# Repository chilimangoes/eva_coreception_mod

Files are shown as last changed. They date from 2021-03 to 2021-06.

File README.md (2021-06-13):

# EVA Coreception Mod

EVA carriage mod for the Creativity ELF/ELF PRO and SainSmart Coreception lines of CoreXY 3D printers

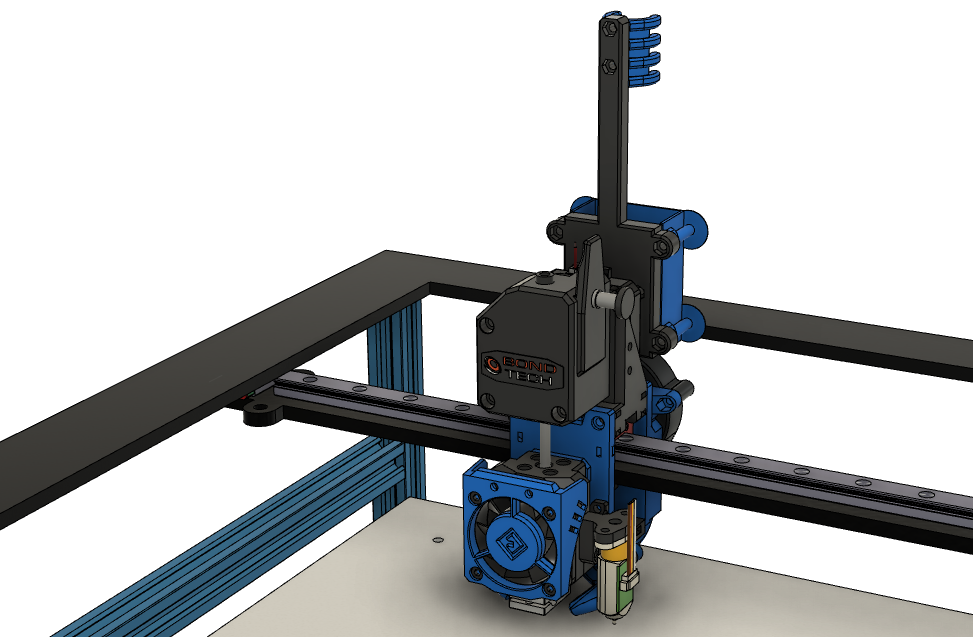
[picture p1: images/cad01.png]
CAD front view


## Overview

This is a mod for the EVA carriage platform to work on the Creativity ELF/ELF PRO and SainSmart Coreception lines of CoreXY 3D printers. However, the changes have been made in such a way as to try to increase the configurability of the tool head, making it adaptable to a wider range of printers. In particular, it should be trivial to adapt to other CoreXY printers with a "halo" design, similar to the ELF variants, such as the Two Trees Sapphire.

Overall print area on my Coreception, with this mod installed, is X=297mm, Y=294mm. I believe that moving the BL Touch to the middle, under the gantry, would increase the X travel by about 10mm. And filing down the M3 bolt hole on the rear blower fan, to allow the bolt head to sit flush with the fan casing, would give another ~3mm of Y travel on the rear.

Check out the [main EVA documentation site](https://main.eva-3d.page/) for more details on the EVA platform, information on printing and postprocessing parts, etc. Feel free to reach out to me on the ELF/Coreception Facebook group with questions or concerns.

## Files

STL files are under the [`/stl`](/stl) folder. You will need to select the appropriate [Face] mount for your hot end - V6, Dragon, or Mosquito. There is also an unofficial mount for the stock MK8 hot end [here](https://contrib.eva-3d.page/hotends/microswiss-mk8/). Start with one of the `"_mirrored"` hot end mounts if you plan on using the BL Touch on the the ELF/Coreception. If you're using the onofficial MK8 mount linked above, you'll need to mirror it yourself. I highly recommend printing out and test fitting everything *thoroughly* before disassembling your existing hot end and carriage. I also recommend printing out a spare set of parts, especially anything that is near or touching the hot end. It might also be a good idea to buy some new, higher quality belts before installing. My stock belts were pretty low quality and chewed up pretty badly by the zip ties used to secure them to the stock carriage.

There are multiple versions of the Y end stop (`end_stop_y_XXmm_offset.stl`) with a range of offsets, to allow people to find tune their Y=0 (I figure there may be manufacturing variances). On my machine, I ended up with either a 6mm or 7mm offset. They're a quick print, so I would recommend starting with the 6mm-8mm offsets, plus the 13mm as a fallback. Once everything is assembled, you can print additional offsets to fine tune, if your machine isn't in the 6mm-8mm offset range.

NOTE: There is a `[Misc] tension_slider_6mm_M3.stl` and `[Misc] tension_slider_6mm_M3_flipped_teeth.stl` for the belt tensioners on the rear. My Coreception uses the `_flipped_teeth` variant, but I would suggest printing out a pair of each, just in case. If you print the wrong ones, you will need to assemble your new carriage backwards, which will cut your Y travel almost in half until you print out the correct ones (don't ask me how I know this 😕). You may also want to print out extras, as these are a somewhat delicate part and can occasionally split when inserting the M3 nuts.

My CAD document for this mod can be accessed [here](https://cad.onshape.com/documents/8374df57f21afb0afda371e1/v/ab8b5f501b92076e0e46f97f/e/99eb3d22b4d42aecd6cd179c) (you may need to create a free OnShape account).

## Mod Details

Here's a brief rundown of my changes, starting with a visual comparison between this mod and the original.

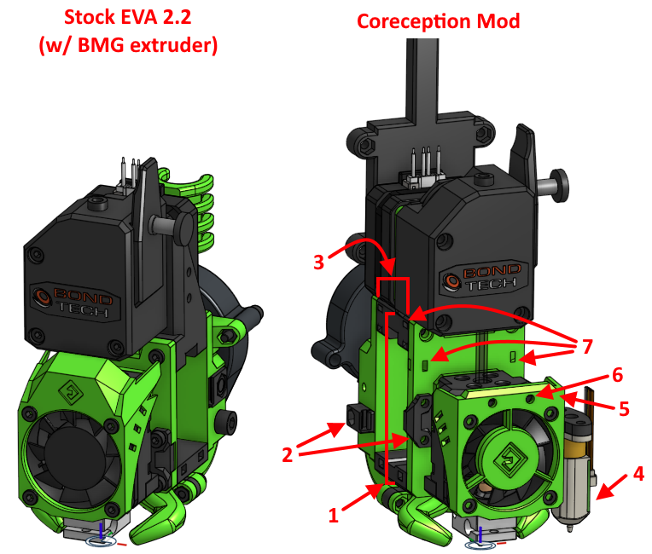
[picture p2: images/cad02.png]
comparison to stock


1. The overall height of the entire carriage was made configurable, and specifically for the ELF/Coreception, the height of the carriage was increased from the default 57mm to 67mm, to allow the hot end to reach down to the print bed without needing to use longer screws or springs to raise the bed.

2. Better configuration of belt size/position/spacing.

    * Belt width is configurable, 6mm or 9mm.
    
    * Left and right belt anchor heights can be configured independently.
    
    * Belt tension sliders in back were changed to use M3 bolts and nuts rather than M5, to allow tension sliders sized for 6mm belts, and also to allow the sliders to be positioned closer to each other, to support the belt geometry on the ELF/Coreception.
    
    * Configured belt offsets to match the stock carriage. Note that this means you may still need to correct the vertical spacing of the idlers on your X gantry. But it also means that if you've already done so, your belt geometry should remain unchanged.

3. Made the carriage depth configurable, and increased the depth to 30mm, from the default 27mm, to fit over the X gantry bar on the ELF/Coreception. I have only modded the top plate for the BMG extruder because that's the extruder I'm using. Honestly, if you're still using the crappy Titan clone that comes with the ELF/Coreception, upgrading to a BMG clone from Trianglelab is one of the best $25 you can spend. However, modding one of the other top plate variants shouldn't be too hard. All that really needs to be done is to mod the top plate depth from the default 27mm to 30m, making sure that the filament path exiting the extruder remains the same.

4. Mirrored versions of all of the current official hot end tool holders (V6, Mosquito, and Dragon) now have mirrored versions to allow putting the BL Touch or other Z probe on the right side of the tool head. While I didn't try using the original configuration, with the probe on the left, it looked like this would cause a problem since the ELF/Coreception home the X axis on the left.

5. A new fan shroud was created that is both lower profile, to fit underneath the halo, and also thicker, to be robust enough for triggering the Y end stop.

6. Mounting holes were added to the shroud for mounting an accelerometer to use Resonance Compensation (A.K.A. Input Shaper) in Klipper. 

7. Zip tie anchor points were added to the front face and both sides of the upper BMG/stepper mount to allow routing wires up and over the gantry, in addition to the existing zip timeouts on the bottom of the carriage. My wires are currently routed underneath the carriage, but I'm considering changing it at some point to route the wires over the top. This would be especially useful for adding a Molex MicroFit connector to allow [easier swapping of tool heads](https://youtu.be/zYscXKBwh0o?t=166).

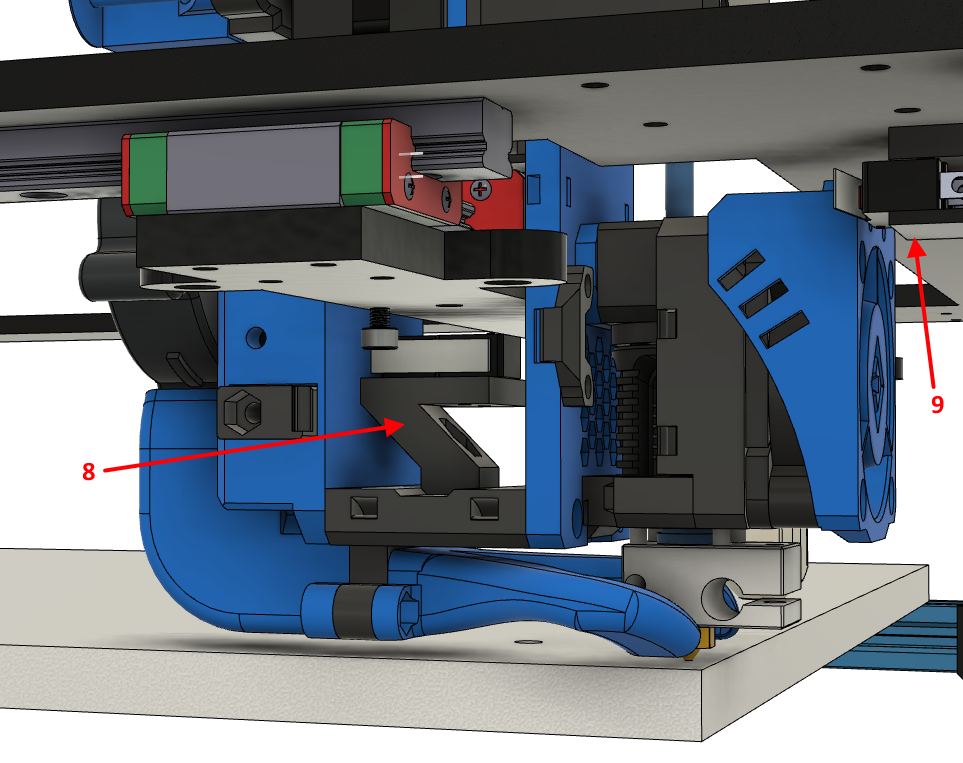
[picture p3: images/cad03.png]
X and Y end stops

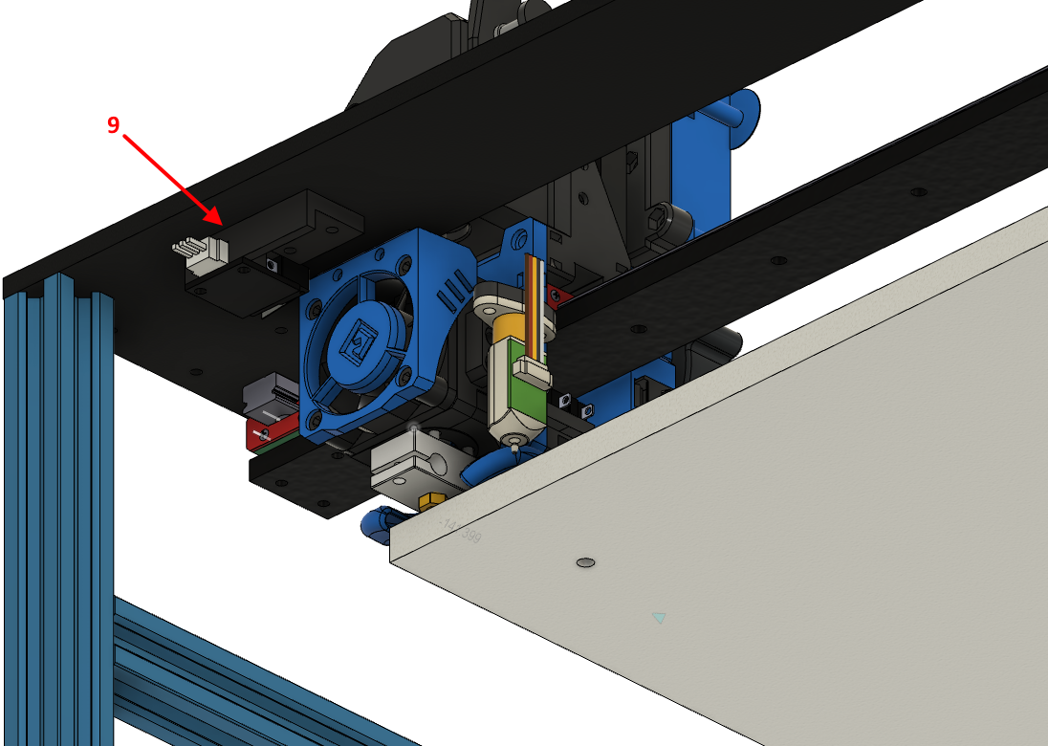
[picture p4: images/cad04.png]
Y end stop location


8. Added an X end stop mount in the center section of the carriage. This mount has 2 sets of holes for mounting the stock end stop switch, and can be adjusted left or right to adjust the X=0 point.

9. Added a new Y end stop mount to maximize the amount of Y travel. This mount uses the existing Y end stop PCB and mounts using the 3 empty M3 holes in the halo, just behind and to the side of where the existing end stop screws into place. See pictures and CAD screenshots.

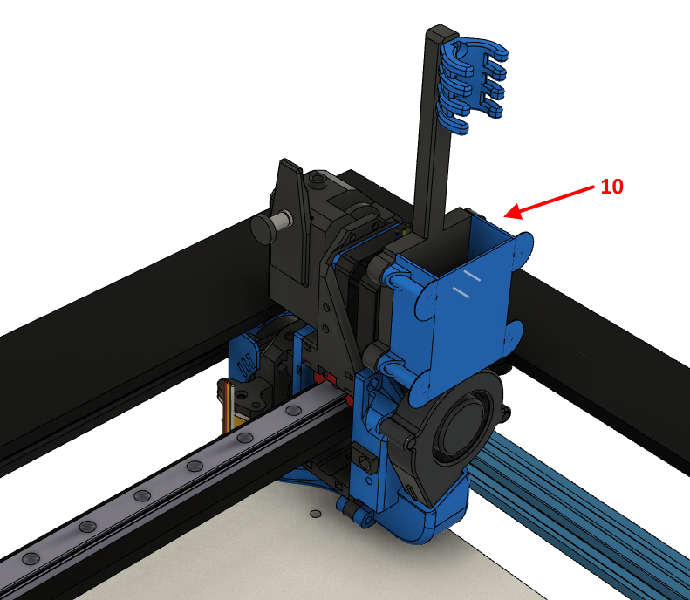
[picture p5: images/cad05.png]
rear view / breakout board mount / VGA cable holder


10. Mount and cover for the stock breakout board, including a tiedown to keep the VGA cable from flopping around.

## ADXL345 / Accelerometer Mounting Options

There are 3 options for mouting an ADXL345 accelerometer for Input Shaping with Klipper. The image below shows mounting options using the new `shroud_low_profile_alt_adxl.stl` file. The original `shroud_low_profile_41mm.stl` will also work for options 1 and 2. Note that this new `shroud_low_profile_alt_adxl.stl` is designed to use with [this style of "M3 X D5.0 X L4.0" heat set inserts](https://www.aliexpress.com/item/4000232858343.html) from a Voron BOM, rather than hex nuts, to make it easier to repeatedly mount and remove the ADXL345. Longer or shorter inserts may work, as well as other styles, but I can't say for sure.

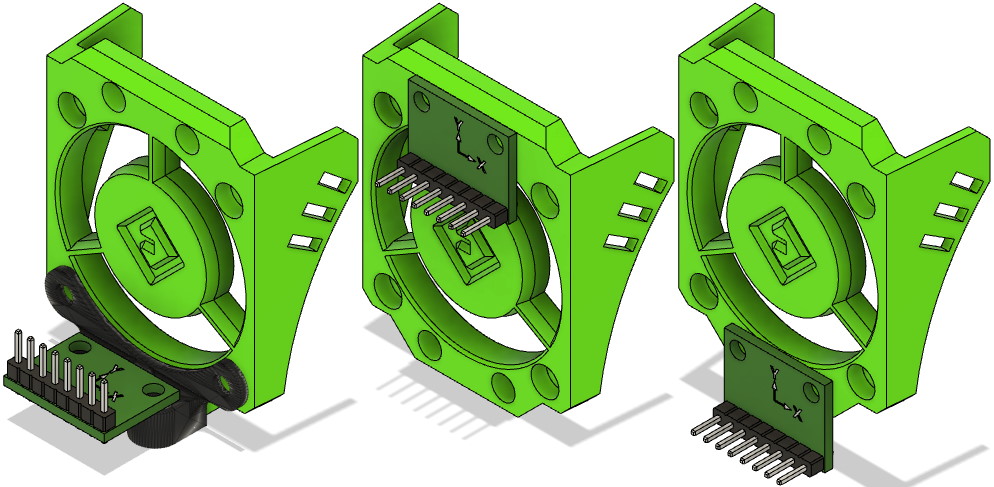
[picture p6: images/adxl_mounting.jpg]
ADXL345 Mounting Options


From left to right:

1. Bottom mount, using the `adxl345_mount4.stl` file, which is  mounted on the front of the shroud using the bottom two holes for the 40 mm hot end fan. This is meant to be a more permanent mounting solution, where you would leave the ADXL345 mounted in place, and simply plug and unplug as needed.

2. Top mount, using either heat set inserts or hex nuts, depending on which verrsion of the shroud you are using. Note that this will position the accelerometer where it would hit the Y end stop, so you would need to print some kind of shield to protect the accelerometer PCB. A better option would be to mount the accelerometer to the bottom of the shroud.

3. Bottom mount, using heat set inserts. Only `shroud_low_profile_alt_adxl.stl` supports this mounting option.

## Photos

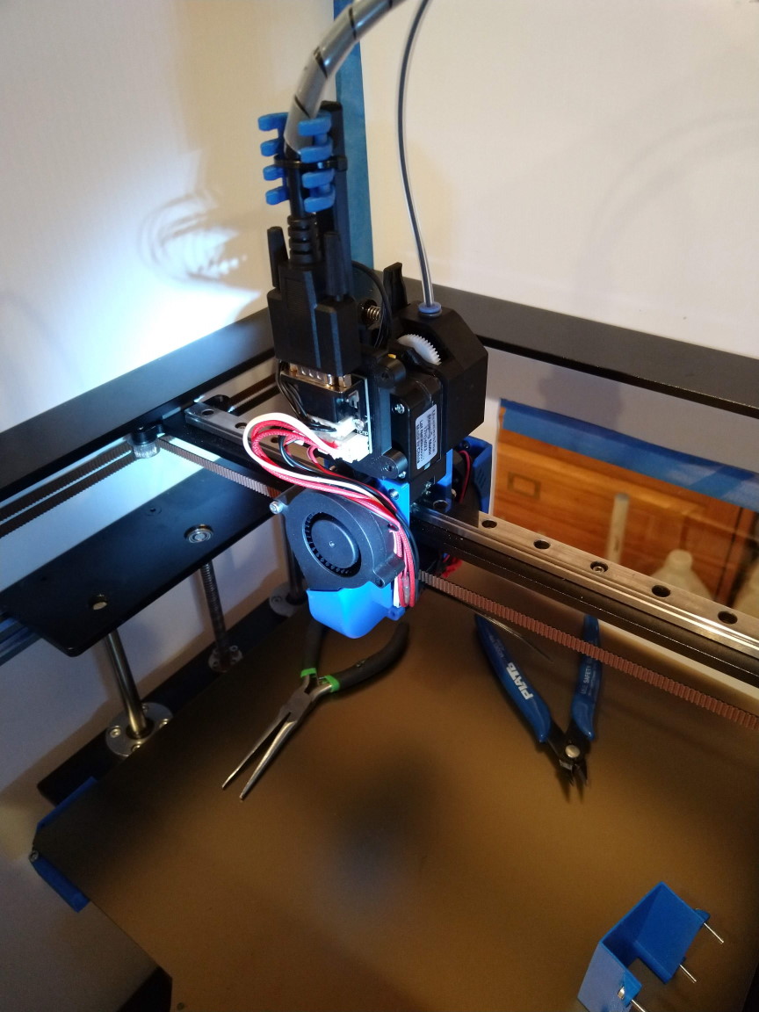
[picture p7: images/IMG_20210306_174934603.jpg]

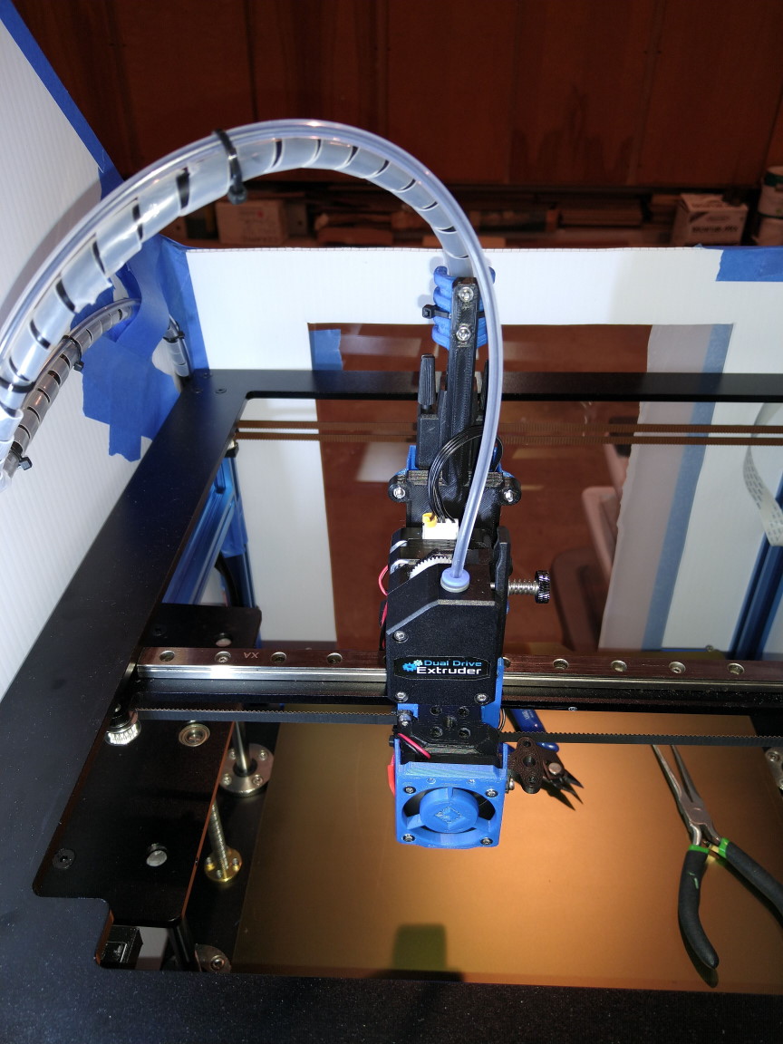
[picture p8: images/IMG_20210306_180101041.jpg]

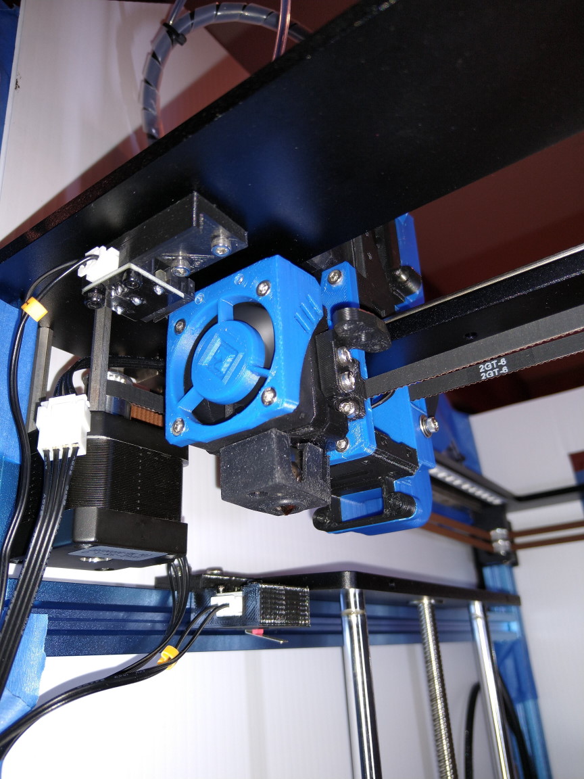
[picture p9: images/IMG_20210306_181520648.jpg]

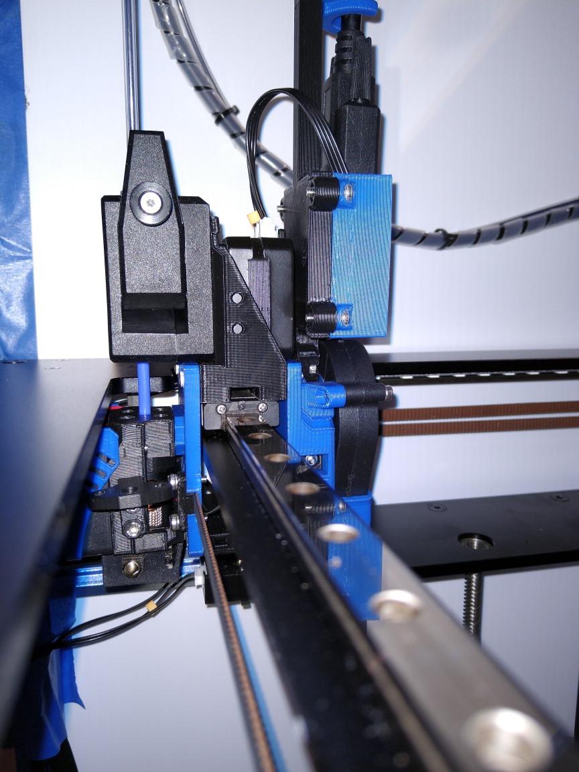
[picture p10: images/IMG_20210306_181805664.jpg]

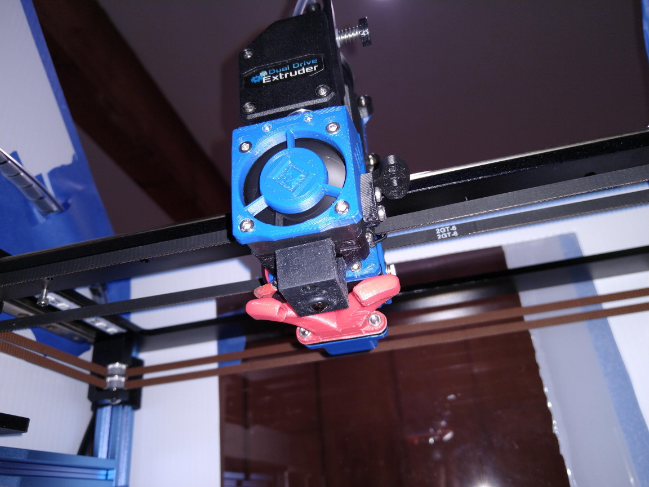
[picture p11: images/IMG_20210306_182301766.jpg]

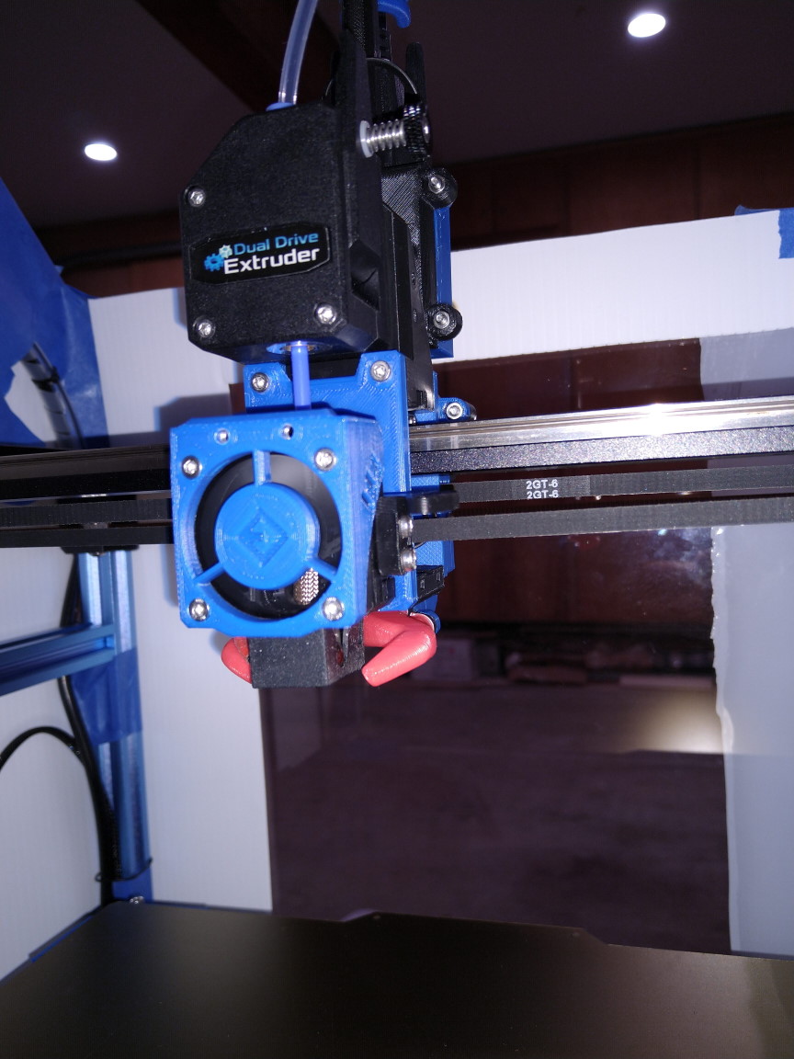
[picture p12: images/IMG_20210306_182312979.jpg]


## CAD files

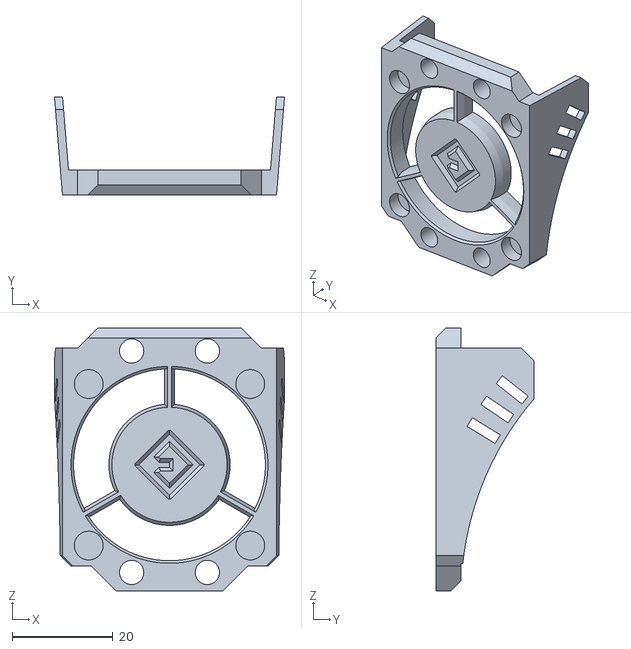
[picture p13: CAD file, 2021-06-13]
stl/shroud_low_profile_alt_adxl.stl
45.6 x 19.5 x 52.1

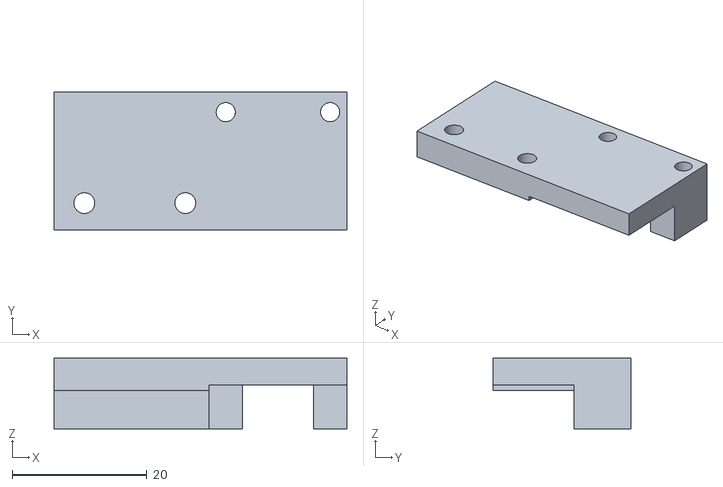
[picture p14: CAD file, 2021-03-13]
stl/end_stop_y_04mm_offset.stl
43.5 x 20.5 x 10.5

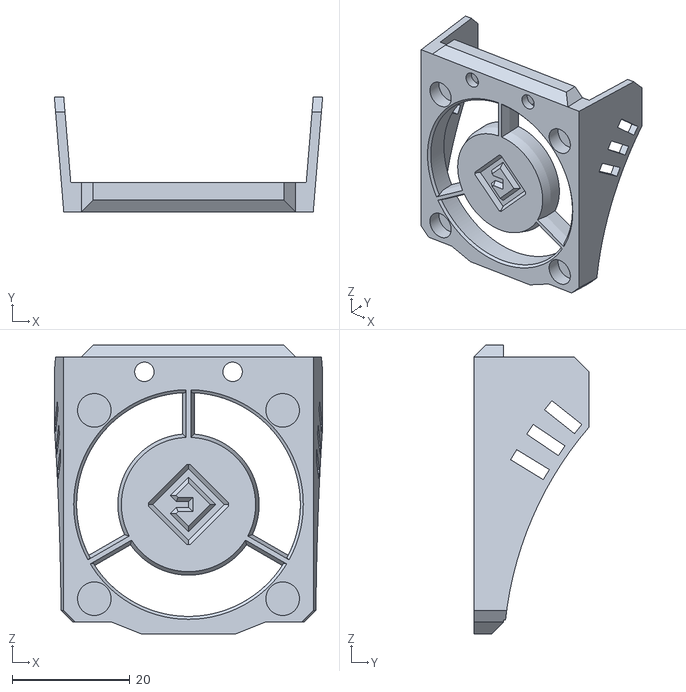
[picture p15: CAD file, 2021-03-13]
stl/shroud_low_profile_41mm.stl
45.6 x 19.5 x 49.1

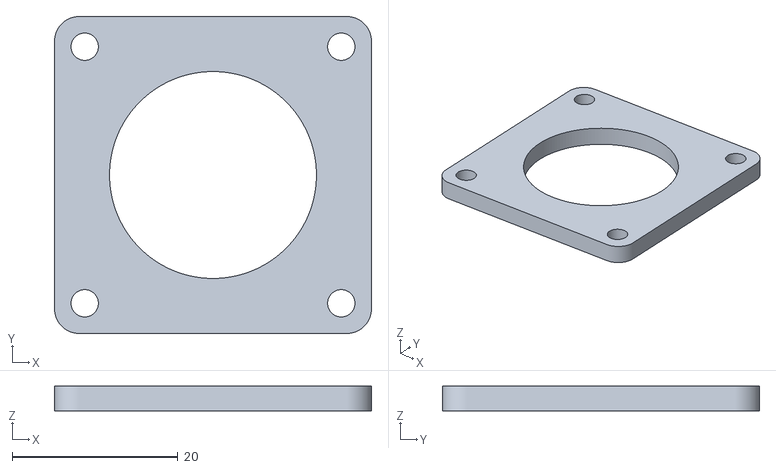
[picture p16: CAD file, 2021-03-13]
stl/nema17_spacer.stl
38.3 x 38.3 x 3.00

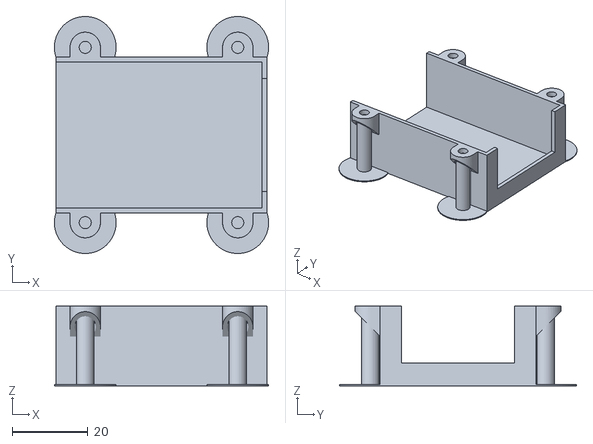
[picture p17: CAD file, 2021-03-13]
stl/breakout_board_cover.stl
56.5 x 62.5 x 21.0

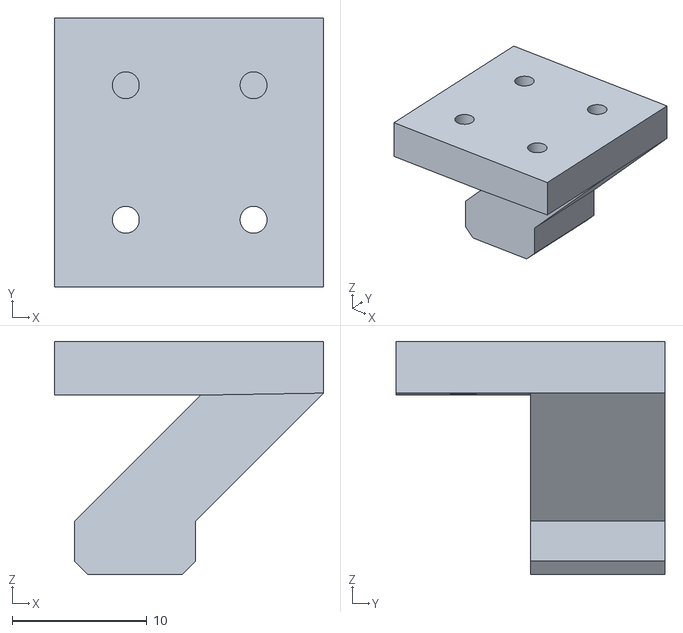
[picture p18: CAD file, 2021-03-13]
stl/end_stop_x.stl
20.0 x 20.0 x 17.3

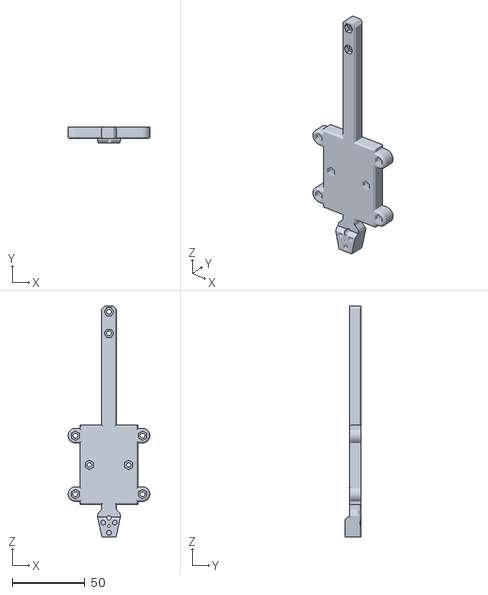
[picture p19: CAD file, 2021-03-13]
stl/coreception_cable_mount.stl
56.2 x 11.0 x 158.8

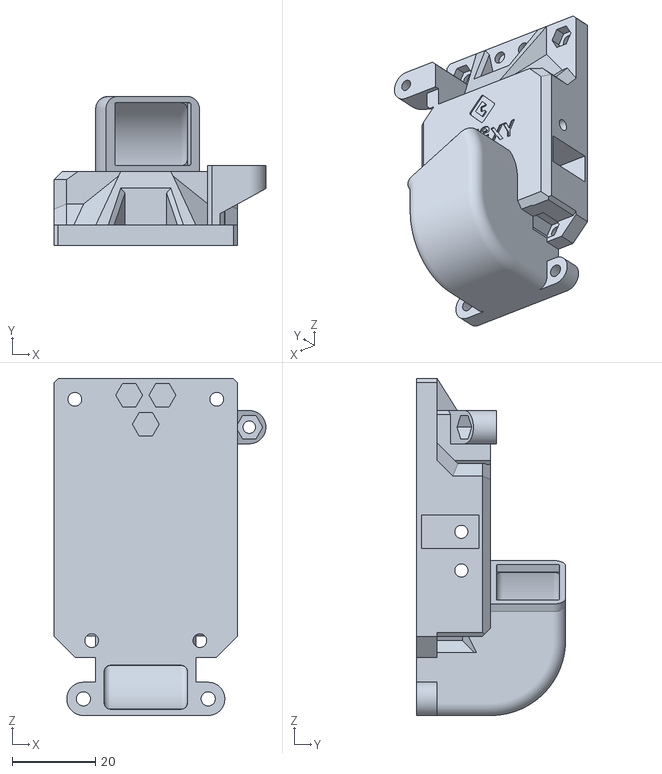
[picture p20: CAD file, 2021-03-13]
stl/[Back] back_corexy.stl
50.9 x 35.9 x 81.0

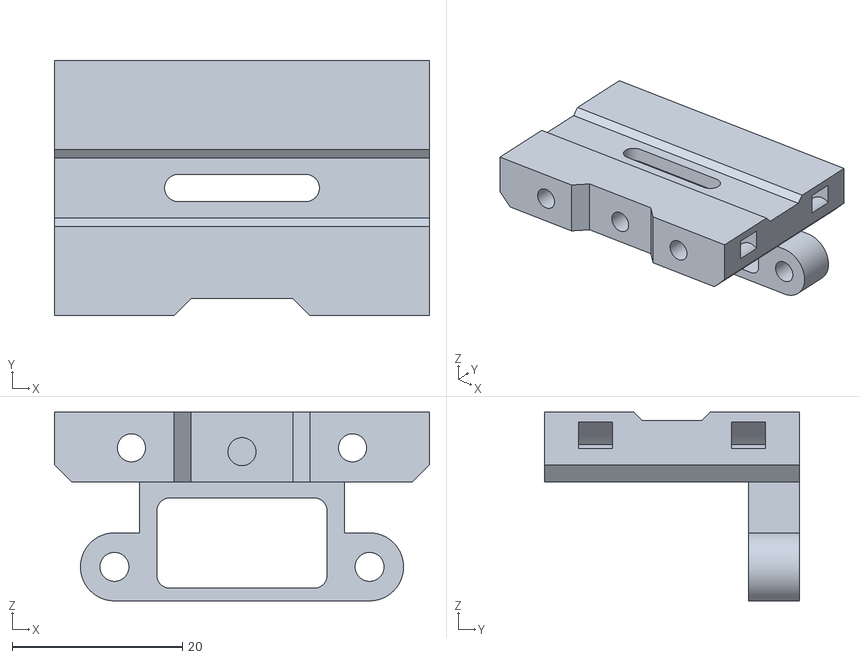
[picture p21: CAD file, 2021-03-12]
stl/[Bottom] Bottoms - Straight.stl
44.1 x 30.0 x 22.2

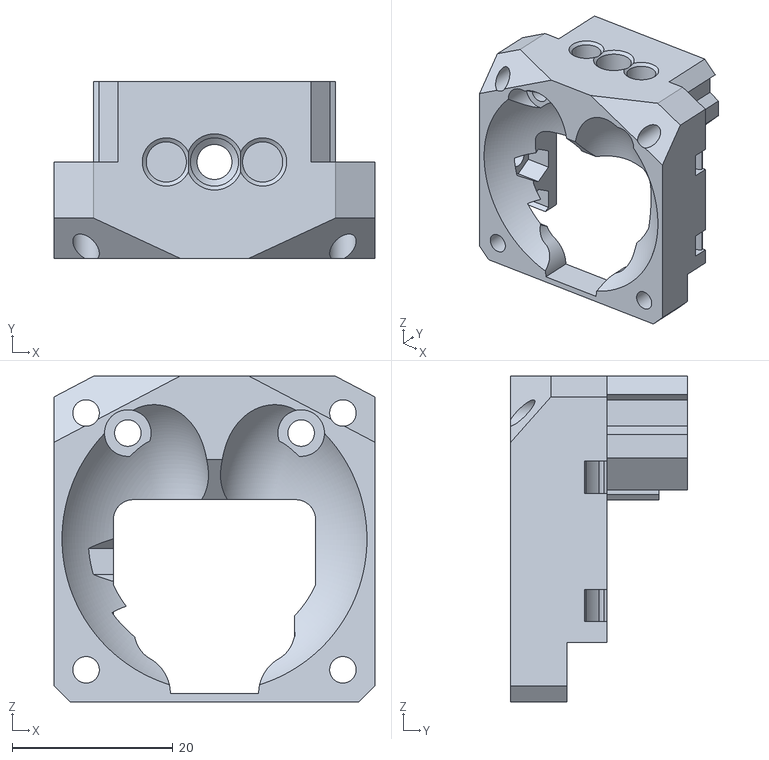
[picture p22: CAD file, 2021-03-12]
stl/[Face] mosquito_face.stl
40.0 x 22.0 x 40.6

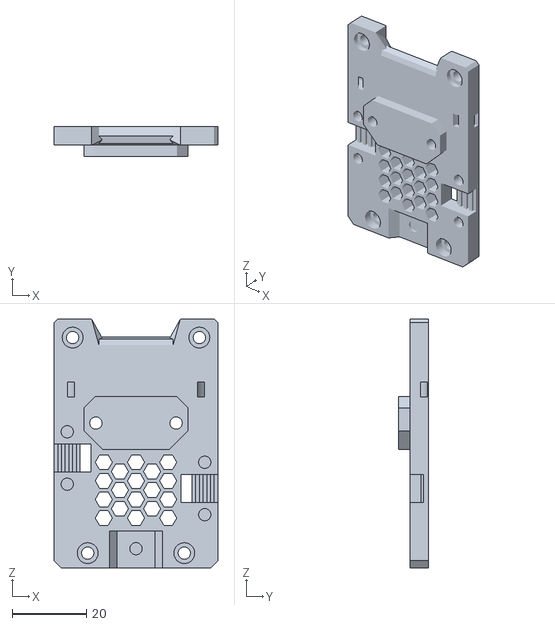
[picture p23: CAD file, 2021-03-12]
stl/[Face] universal_face.stl
44.1 x 8.00 x 67.0

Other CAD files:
stl/end_stop_y_05mm_offset.stl
stl/end_stop_y_09mm_offset.stl
stl/end_stop_y_13mm_offset.stl
stl/end_stop_y_08mm_offset.stl
stl/end_stop_y_10mm_offset.stl
stl/end_stop_y_07mm_offset.stl
stl/end_stop_y_06mm_offset.stl
stl/[Face] dragon_face.stl
stl/[Face] dragon_face_mirrored.stl
stl/[Face] dragon_support_5.7mm.stl
stl/[Face] face_belt_grabber.stl
stl/[Face] mosquito_face_mirrored.stl
stl/[Face] mosquito_support.stl
stl/[Face] v6_face.stl
stl/[Face] v6_face_clamp.stl
stl/[Face] v6_face_mirrored.stl
stl/[Face] v6_support_5.7mm.stl
stl/[Misc] tension_slider_6mm_M3.stl
stl/[Misc] tension_slider_6mm_M3_flipped_teeth.stl
stl/[Top] top_bmg_mgn12.stl
stl/adxl345_mount4.stl
stl/bl_touch_mount.stl

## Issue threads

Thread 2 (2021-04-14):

Breakout board cover

hakimio, 2021-04-14:
Breakout board cover seems to have one "minor" issue: it's impossible to put the screws in/holes are covered. Can you share the cover you are using?

hakimio, 2021-04-14:
Ok, I guess, it's just support which you supposed to break-off.

Closed 2021-04-14.

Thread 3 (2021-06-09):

[Question] Verical pulley alignment

hakimio, 2021-06-09:
Hi @chilimangoes

I am wondering what vertical distances did you use when positioning belt holders/clamps on EVA carriage. The original pulleys from the factory seem to be extremely misaligned: the lower pulleys on X gantry way higher than the pulleys in the front of the printer. The lower pulley in front is around 29mm from the Y gantry and the one on X gantry is around 27mm from the Y gantry. I am currently designing pulley holder bracket for holding larger pulleys in front of the printer (instead of the metal original part) and I am trying to decide what vertical pulley distances I should use. Have you installed bigger pulleys and proper shoulder bolts? What measurements did you use?

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

chilimangoes, 2021-06-12:
Hi @hakimio

Sorry, I just saw this today. Yeah, the lower pulleys are pretty misaligned from factory. I tried to line my belt anchor locations as closely as I could with the idler pulleys on the front of the printer. That way, when I finally get around to replacing the idlers on the gantry, I can line those up with the front idlers and everything should be even.

For reference, here are the measurements I used for the anchor locations. Vertical measurements are from the bottom of the gantry to the centerline of the anchor point.

Upper belt: 5.4 mm to centerline
Lower belt: 15.1 mm to centerline

Visual example:
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

And from my measurements, you would add ~19 mm to get the vertical distance from the under side of the halo to the centerlines of the pulleys. Hopefully that all makes sense.

I still plan to replace the pulleys and use shoulder bolts, but it hasn't been a priority because it's printing fine and I've been crazy busy with other projects. I don't have any plans to use bigger pulleys though. I just plan on using the same size idlers as stock because I got a bunch of them for my Voron build. On the gantry, I plan to use F695 bearings in place of the front idlers - again, because that's what the Voron uses for smooth idlers.

hakimio, 2021-06-13:
Makes perfect sense. Thank you for detailed explanation.

Just one more small question: have you installed or do you plan to install `adxl345` accelerometer? How is it supposed to be mounted on your EVA mod?

chilimangoes, 2021-06-13:
Yes! Which actually reminded me that I had designed a newer version of the fan shroud, with additional mounting holes on the bottom for an ADXL345. I've uploaded the new shroud and updated the README with information on 3 different accelerometer mounting options.

Here:
https://github.com/chilimangoes/eva_coreception_mod/blob/main/README.md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

hakimio, 2021-06-14:
Thanks. Which mount are you using yourself?

chilimangoes, 2021-06-14:
I'm currently using option 1. I plan to switch to option 3, but I haven't printed the new shroud yet.

Closed 2021-06-14.

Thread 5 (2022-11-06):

The file "Breakout Board Mount" is missing.

Majix007, 2022-11-06:
There is a file missing. I can find the "Breakout Board Cover", and the "Cable Holder". But the "Breakout Board Mount" is missing. Can you add this file please?

Majix007, 2022-11-06:
Found it. It's called "coreception cable mount".

Closed 2022-11-06.

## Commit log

2021-03-12 added CAD screenshots
2021-03-12 added STL files
    [[Back] back_corexy.stl, [Bottom] Bottoms - Straight.stl, [Face] dragon_face.stl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]
2021-03-13 Updated `[Back] back_corexy.stl`. I had inadvertently included an older version with the lower belt offset about 1.5mm too low.
    [[Back] back_corexy.stl]
2021-03-13 added missing stl files
    [breakout_board_cover.stl, coreception_cable_mount.stl, end_stop_x.stl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]
2021-06-13 Add alternate shroud with alternate ADLX345 mounts
    Added alternate shroud with heat set insert holes on top and bottom for mounting ADXL345
    [shroud_low_profile_alt_adxl.stl]
2021-06-13 ADLX345 mounting pic
2021-06-13 Update README with accelerometer mounting options
